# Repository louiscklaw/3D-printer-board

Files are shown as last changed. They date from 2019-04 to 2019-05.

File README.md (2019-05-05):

### PCB tryout for louis 3d printer
* PCB look like:
	* front:
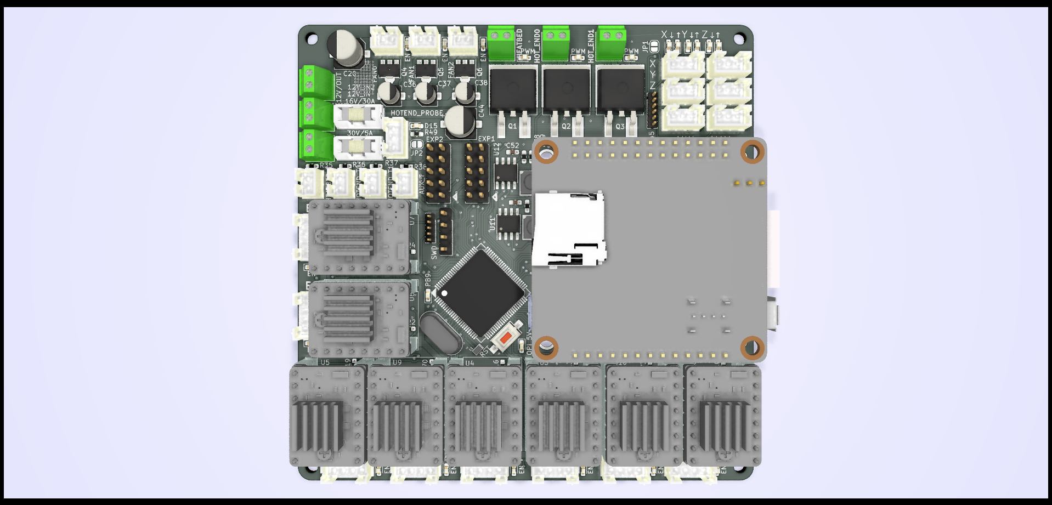
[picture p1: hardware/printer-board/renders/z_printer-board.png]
PCB Front Front
	

	* back:
	PCB Back Back

### to initialize the stm32 with klipper firmware
* to flash klipper with stm32duino: 
    * `wget 'https://github.com/rogerclarkmelbourne/STM32duino-bootloader/raw/master/binaries/generic_boot20_pc13.bin'`
    * `st-flash /home/logic/_del/7/generic_boot20_pc13.bin 0x8000000`
    * `dfu-util -d 1eaf:0003 -a 2 -R -D out/klipper.bin`

* to flash klipper by st-link
    * `st-flash write klipper.out 0x8000000`

ref: https://github.com/KevinOConnor/klipper/blob/master/docs/Bootloaders.md

### TODO on this REV:
- [x] tidy
- [x] need to confirm about ~~PC13~~ PB9 as debug pin

### Design goal on REV1:
- [x] ~~10~~ 8 channels and ~~10~~ 8 stepper motors
    - [x] x
    - [x] y
    - [x] z0,z1,z2,z3
    - [x] e0,e1,~~e2,e3~~

- [x] ~~5~~ 3 channels PWM control(high power) heaters
    - [x] hotend0, hotend1, ~~hotend2, hotend3~~
    - [x] heatbed

- [x] ~~5~~ 3 channels PWM control(low power) fans
    - [x] hotend0, hotend1, ~~hotend2, hotend3~~
    - [x] heatbed

- [x] 6 and ~~4~~ 1 DI
    - [x] x,y,z min
    - [x] x,y,z max
    - [x] ~~4 misc~~ 
    - [x] PROBE support

- [x] ~~5~~ 4 + 1  AI(temperature sensors)
    - [x] hotend0,hotend1,~~hotend2,hotend3~~, AUX
    - [x] heatbed
    - [x] PCB temperature self monitoring

### Board source current estimation (**Rough/TBC**):
* stepper motors = 10 * 0.5A ~= 5A
* heatbed = 150W/12 ~= 12A
* hotends = 2 * 20W = 80W ~= 3A

* 12 + 5 + 3 = 20A
* guess taking 0.5 as Diversity factor => 10A

### Thing TODO on next REV:
- [ ] replacement for Orange Pi as too big in size
- [ ] I2C output
- [ ] possibily some digital output channel
- [ ] possibily some SSR channel

### Misc:
* pinmapping
    * https://github.com/KevinOConnor/klipper/blob/master/docs/stm32f1.md

* Constrains on STM32:
> When using serial, the UART used for communication with the host is fixed to pins PA9 (TX) and PA10 (RX). 
> When using USB, the PA11 (D-) and PA12 (D+) pins are reserved. 
> The USB code assumes that PA12 (D+) has a fixed pullup resistor attached to it.

> SWD pins (PA13/PA14) are enabled for debugging and cannot be used for any I/O. 
> SPI uses pins PB13/PB14/PB15, but the pins can be used as general I/O if SPI is not used.
> Digital I/O

> All pins that aren't part of the fixed set can be used for digital I/O. 
> Pins are referred to by their primary name, e.g. PA1. 
> Do not try to use Arduino pin aliases in your configuration. 
> See ST's datasheets for more details. 
> The STM32Duino wiki has more info on the popular "Blue Pill" board.
> Analog inputs

> All ADC-capable pins can be used as analog inputs with the same naming as digital I/O pins. 
> Small packages MCUs (e.g. LFQP48) have 10 channels (PA0-PA7, PB0-PB1), while larger package devices have 16 channels (PA0 PA7, PB0-PB1, PC0-PC5).

> SPI
> SPI uses pin PB13 (SCK), PB14 (MISO) and PB15 (MOSI). The clock speed range is 0.15..18 MHz.  Chip select pins do not have any restrictions.

ref: https://github.com/KevinOConnor/klipper/blob/master/docs/stm32f1.md

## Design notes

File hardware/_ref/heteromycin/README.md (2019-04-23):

# Heteromycin - 3D printer board

[Join us on Discord!](https://discord.gg/f4dmGsn)

Heteromycin is a 3D printer controller that aims to provide a full stack user
experience around Octoprint / Marlin using a custom designed board that
integrates a Raspberry Pi 3 or Zero W. It will also provide a solid, powerfull
hardware by utilizing quality components, a STM32 32bit MCU and powerfull
TMC5160 or TMC2160 driver (SD / SPI mode).

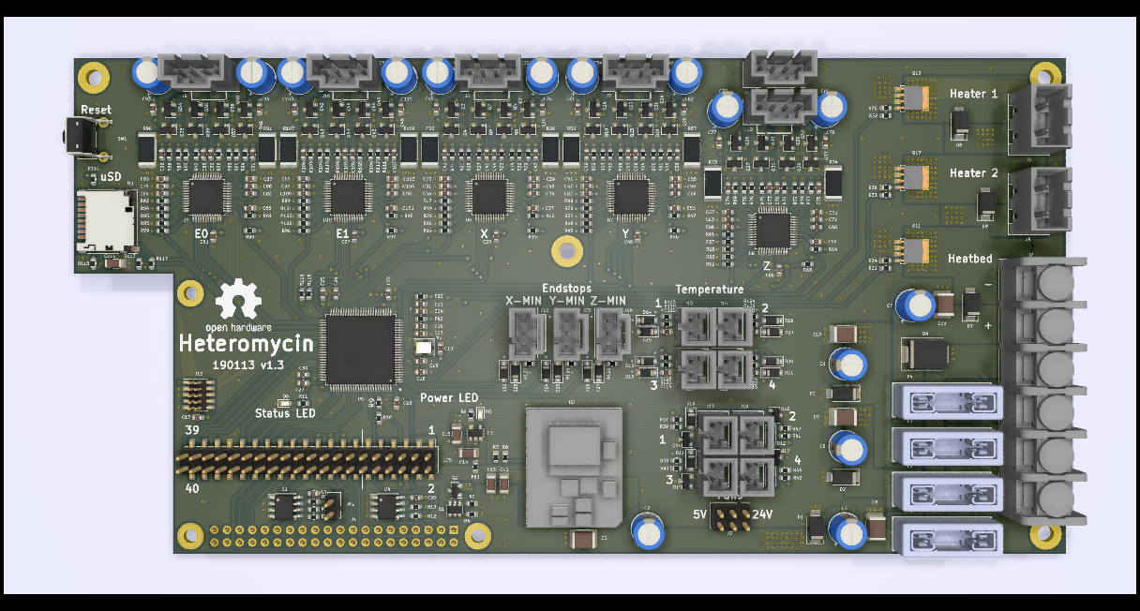
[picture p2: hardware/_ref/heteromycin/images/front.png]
heteromycin version 1.0


## Features

* 32bit STM32H743VI 400Mhz / 1024KiB RAM / 2MiB Flash MCU / 4 KiB EEPROM
* Integrated Raspberry Pi 3 / Zero W HAT connector as the main user interface
* Integrated DC/DC switching module for 5V / 3.3V power supply
* 5x TMC5160 or TMC2160 stepper driver with 8x external Power MOSFET each
* 3x high power MOSFET for heating (2x heater, 1x heatbed, 24V)
* 4x low power MOSFET for fans (5V or 24V)
* 40 pin external connector for STM32 and Pi GPIO pins
  * GPIO
  * PWM
  * UART
  * SPI
  * I2C
  * 3.3V / 5V / GND for external power consumption
* Micro SD Card for storing GCODE files (directa MCU access)
* Designed for a 24V power supply
* Automotive fuses
* Quality connectors
* Octoprint plugin for flashing the firmware of the board (STM32)

## Roadmap

* Hardware
  * [x] Describe the general functionality and select the main components
  * [x] Draw the schematics of the PCB
  * [x] Placement & routing of the PCB
  * [ ] Production of a development board
  * [ ] Testing the PCB
  * [ ] Repreat until hardware is finished
* Software
  * [x] Write arduino core board definition once first PCB design is finished
  * [ ] Write PIN file for Marlin
  * [ ] Test board (esp. the TMC*160 driver)
  * [ ] Octoprint plugin for firmware upgrade
  * [ ] STM32flash rewrite (fix I2C and add SPI, maybe rewrite in rust)
  * [ ] Create a script / image with Octoprint with the plugin / tools
  preinstalled
  * [ ] Documentation

## Alternative Parts

### Stepper driver

You can use both TMC5160 or TMC2160 as the stepper driver, since they both are
functionally / pin equal when used in SD / SPI-Mode.

It doesn't mater choosing one over the other, other than price and availability.

Fine tuning of the MOSFET driver may be necessary.

## License

The hardware is licensed under CERN OHL version 1.2.
The software is licensed under GNU GPL v3.

The files under PCB/packages3d are excluded from this license and are provided
under fair use terms for this open-source project.

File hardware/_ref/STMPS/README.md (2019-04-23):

STMPS
=====

**STMPS** is a WIP 3d printer board based around the STM32f411, with inspiration and guidance
from the Printrboard, RAMPS 1.4, and the RepRap project.

**ALPHA-3**

a3

This board is intended to work with Ambroz Bizjak's astonishingly fantastic 
[aprinter](https://github.com/ambrop72/aprinter) firmware. Configuration files and guidance will be
provided once the board is further along.

STMPS is open source hardware, licensed under CC BY-SA. Copyright (C) 2016 Greg Lincoln.

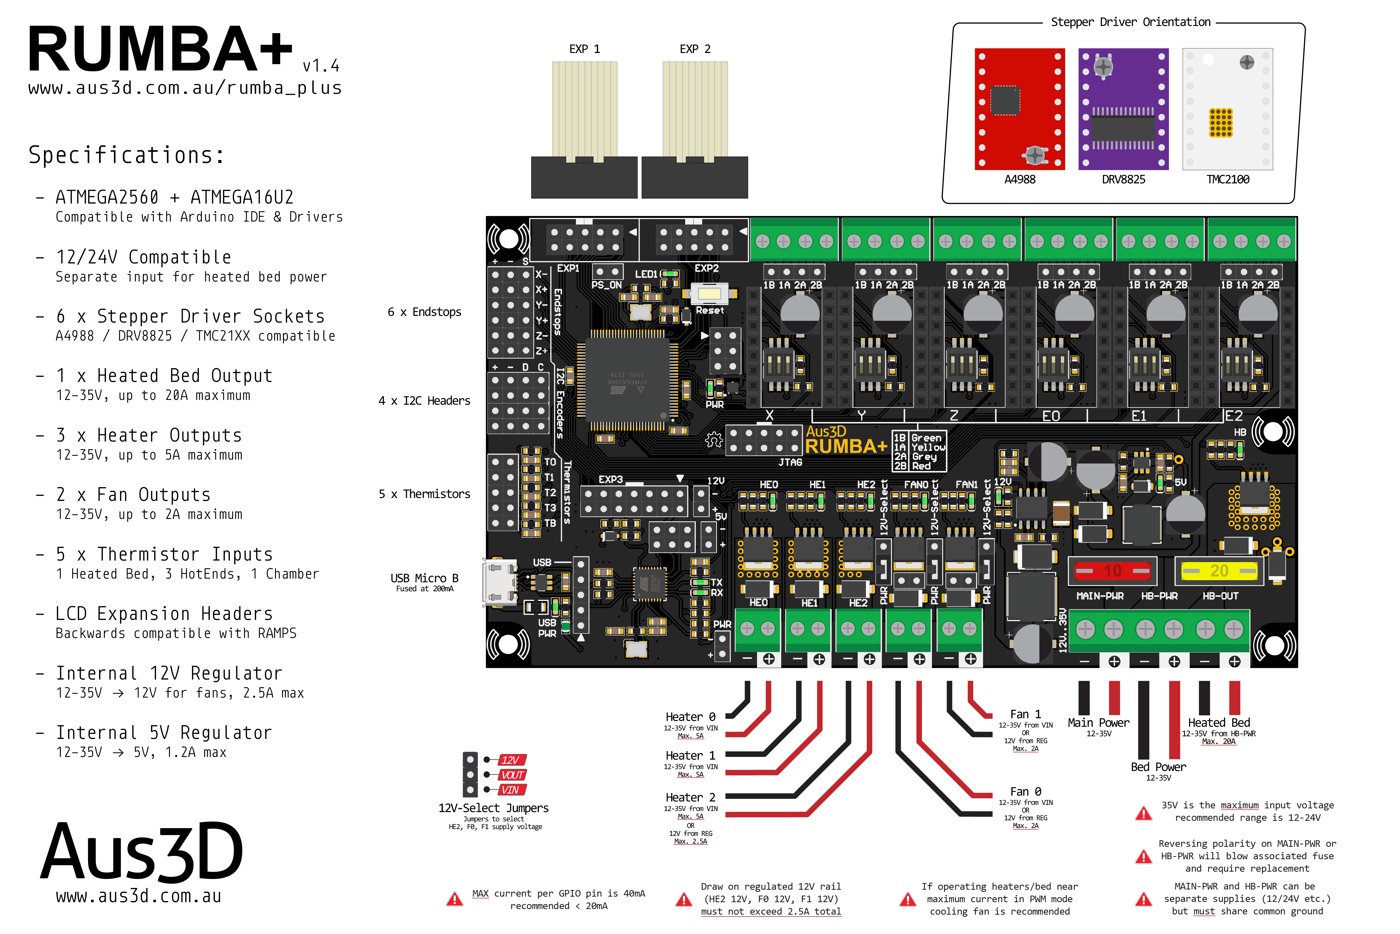
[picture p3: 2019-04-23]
hardware/_ref/RUMBA-Plus/Images/pinOut.png

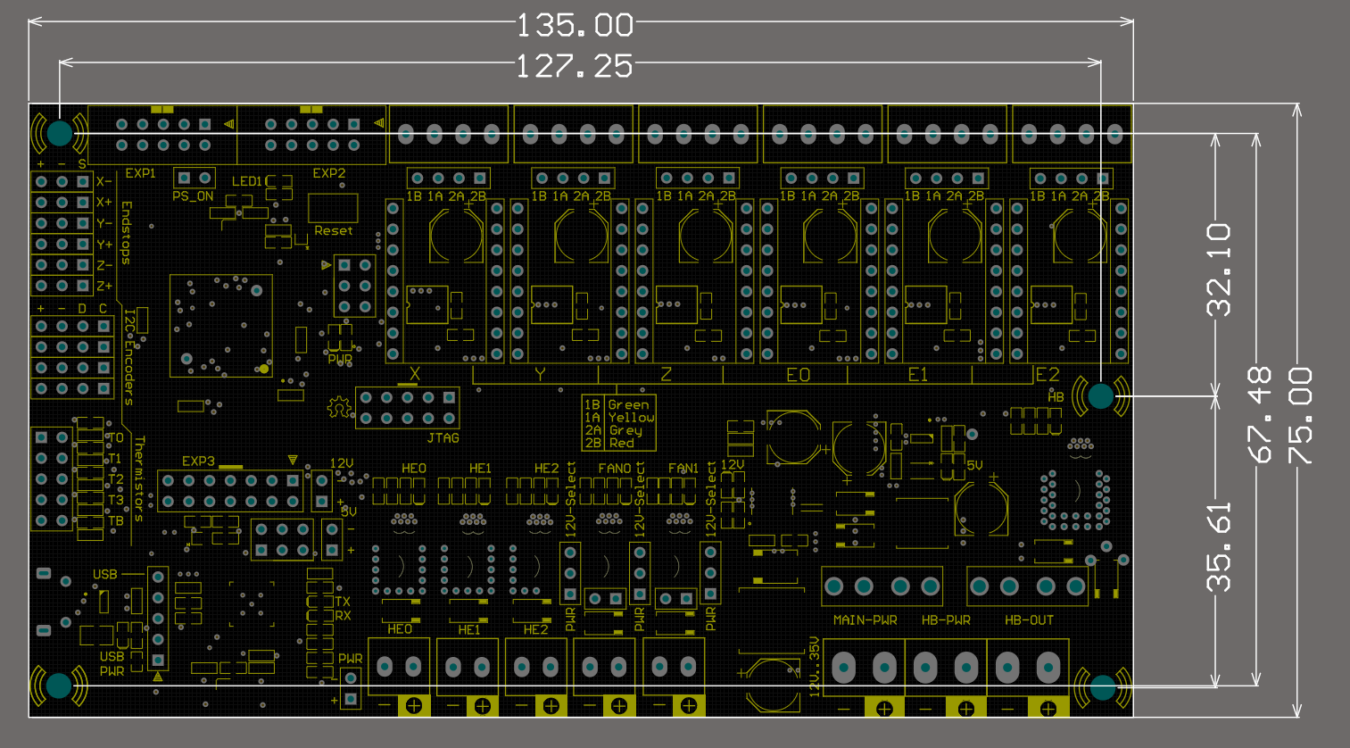
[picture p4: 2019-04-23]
hardware/_ref/RUMBA-Plus/Images/BoardMountingDimension.png

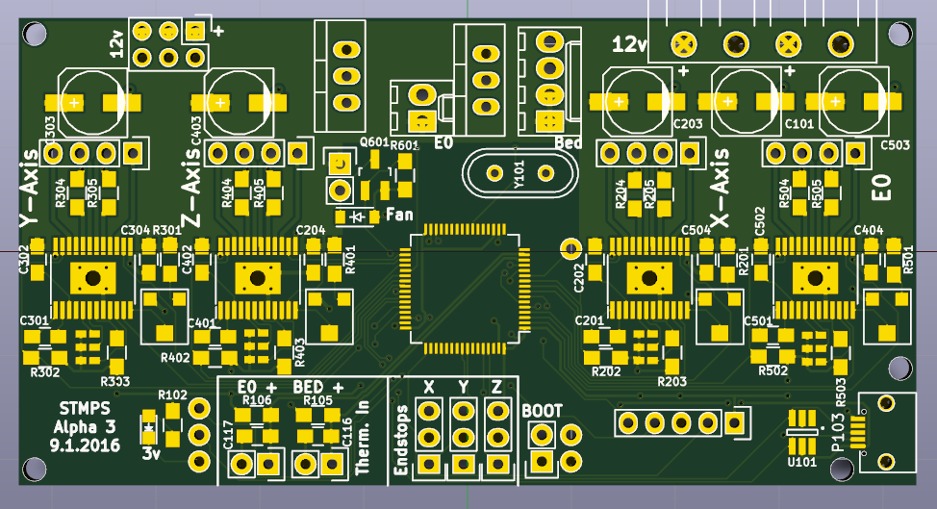
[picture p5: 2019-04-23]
hardware/_ref/STMPS/img/stmps-a3.png

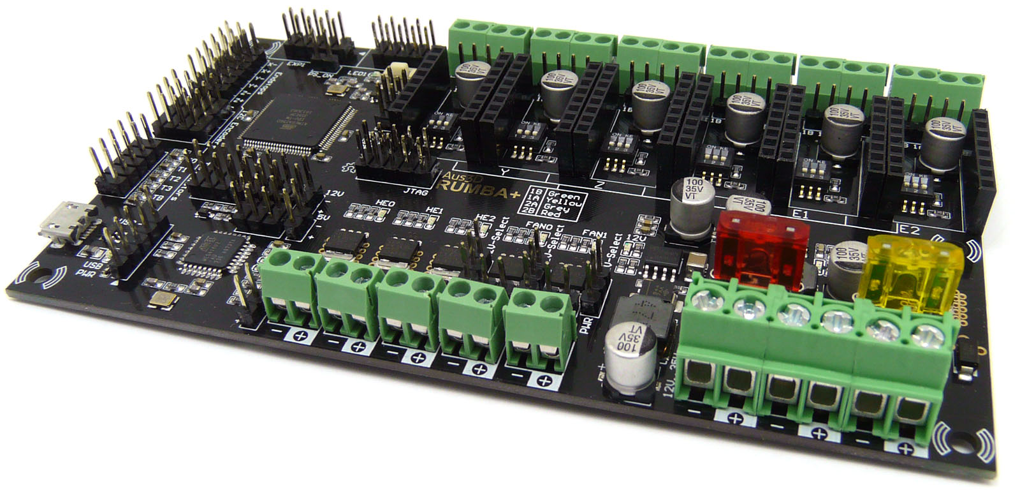
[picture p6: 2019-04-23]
hardware/_ref/RUMBA-Plus/Images/boardPhoto.jpg

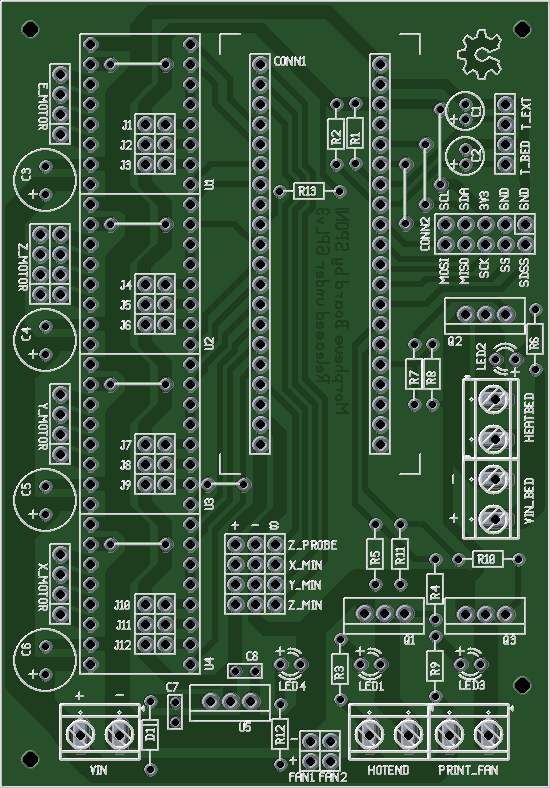
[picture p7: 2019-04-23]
hardware/_ref/Morpheus-STM32/documents/board.png

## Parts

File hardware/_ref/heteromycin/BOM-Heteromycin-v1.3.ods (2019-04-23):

Reference(s) | Value | Mft. Nr. | Digikey Nr. | Mouser Nr. | LCSC Nr. | Qty | Footprint | Note | Datasheet
C1, C16, C17, C18, C19, C22, C23, C24, C25, C26, C27, C29, C31, C33, C39, C40, C47, C49, C55, C56, C63, C65, C71, C72, C79, C81, C87, C88, C95, C97, C103, C104, C112, C113, C114, C115 | 100nF | C0603C104M5RACTU | C0603C104M5RACTU | 81-GCM188L81H104KA7D | C42998 | 36 | Capacitor_SMD:C_0603_1608Metric | Min. 35V | ~
C2, C4, C5, C6, C7, C32, C38, C48, C54, C64, C70, C80, C86, C96, C102 | 100uF | 860020573008 | 732-8942-1-ND | 710-860020573008 |  | 15 | Capacitor_SMD:CP_Elec_6.3x5.7 | Min. 35V
C3, C8, C9, C10, C11 | 100nF | VJ1812Y104KXBAT | 478-4009-1-ND | 77-VJ1812Y104KXBAT | C106148 | 5 | Capacitor_SMD:C_1812_4532Metric | Min. 35V
C12, C14 | 22uF | LMK316ABJ226KL-T | 1276-1771-2-ND | 963-LMK316ABJ226KL-T | C92818 | 2 | Capacitor_SMD:C_1206_3216Metric | Min. 6V | ~
C13 | 100nF | VJ1206Y104JXQCW1BC | 732-12245-1-ND | 77-VJ1206Y104JXQCBC | C313097 | 1 | Capacitor_SMD:C_1206_3216Metric | Min. 6V | ~
C15, C111 | 10uF | EMK316BJ106MD-T | 1276-2877-1-ND | 963-EMK316BJ106MD-T | C50691 | 2 | Capacitor_SMD:C_1206_3216Metric | Min. 6V | ~
C20, C21 | 1uF | 885012106022 | 1276-6524-1-ND | 710-885012106022 | C95843 | 2 | Capacitor_SMD:C_0603_1608Metric | Min. 6V | ~
C28, C30, C35, C36, C51, C52, C67, C68, C83, C84, C99, C100 | 2.2uF | CGB3B1X5R1C225M055AC | 587-4861-1-ND | 810-CGB3B1X5R1C225MC | C106832 | 12 | Capacitor_SMD:C_0603_1608Metric | Min. 16V | ~
C34, C50, C66, C82, C98 | 22nF | C0603C223K1RACTU | 399-3476-1-ND | 80-C0603C223K1R | C77443 | 5 | Capacitor_SMD:C_0603_1608Metric | Min. 100V | ~
C37, C45, C46, C53, C61, C62, C69, C77, C78, C85, C93, C94, C101, C109, C110 | 470nF | GMK107B7474KAHT | 445-172475-1-ND | 963-GMK107B7474KAHT | C296719 | 15 | Capacitor_SMD:C_0603_1608Metric | Min. 35V | ~
C41, C42, C43, C44, C57, C58, C59, C60, C73, C74, C75, C76, C89, C90, C91, C92, C105, C106, C107, C108 | 220nF | GMK107BJ224KAHT | 490-12546-1-ND | 963-GMK107BJ224KAHT | C123521 | 20 | Capacitor_SMD:C_0603_1608Metric | Min. 35V | ~
D1, D2, D3 | SMAJ28A | SMAJ28A-13-F | SMAJ28A-FDICT-ND | 621-SMAJ28A-13-F | C353458 | 3 | Diode_SMD:D_SMA |  | https://www.mouser.de/datasheet/2/240/Littelfuse_TVS_Diode_SMAJ_Datasheet.pdf-540740.pdf
D4 | S3A-13-F | S3A-13-F | S3A-FDITR-ND | 621-S3A-F | C264105 | 1 | Diode_SMD:D_SMC |  | https://www.mouser.de/datasheet/2/115/ds16005-37880.pdf
D5 | LTST-C194KGKT | LTST-C194KGKT | 160-1834-1-ND | 859-LTST-C194KGKT | C125098 | 1 | LED_SMD:LED_0603_1608Metric |  | ~
D6 | LTST-C194KSKT | LTST-C194KSKT | 160-1836-1-ND | LTST-C194KSKT | C84268 | 1 | LED_SMD:LED_0603_1608Metric |  | ~
D7, D8, D9 | SK310A-LTP | SK310A-LTP | SK310A-LTPMSCT-ND | 833-SK310A-LTP | C91474 | 3 | Diode_SMD:D_SMA |  | https://www.mouser.de/ProductDetail/Micro-Commercial-Components-MCC/SK310A-TP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
D10, D11, D12, D13, D14, D15, D16, D17, D18, D19, D20, D21, D22, D23, D24, D25, D26, D27 | BAT54GWJ | BAT54GWJ | 1727-7328-1-ND | 841-BAT54GWJ |  | 18 | Diode_SMD:D_SOD-123 |  | https://www.mouser.de/datasheet/2/916/BAT54GW-1318921.pdf
F1, F2, F3, F4 | 3557-2 | 3557-2 | 36-3557-2-ND | 534-3557-2 |  | 4 | heteromycin:KEYSTONE-FUSE-3557-2 |  | ~
FB1, FB2, FB3 | MPZ1608S221A | MPZ1608S221A | 445-1565-2-ND | 810-MPZ1608S221A | C76815 | 3 | Resistor_SMD:R_0603_1608Metric |  | https://www.mouser.de/datasheet/2/400/eads_commercial_power_mpz1608_en-923650.pdf
J1 | M20-7832046 | M20-7832046 | 952-2150-ND | 855-M20-7832046 |  | 1 | Connector_PinSocket_2.54mm:PinSocket_2x20_P2.54mm_Vertical
J2 | 4DB-P108-06 | 4DB-P108-06 | 4DB-P108-06 | 571-214376679 |  | 1 | heteromycin:4DB-P108-06 | Alternative: OSTYK42106030 | https://www.mouser.de/datasheet/2/418/NG_CD_2-1437667-4_N8-639207.pdf
J3, J4 | 039531-1002 | 039531-1002 | WM7837-ND | 538-39531-1002 |  | 2 | heteromycin:39531-1002 |  | ~
J5 | 68602-406HLF | 68602-406HLF | 609-4934-ND | 649-68602-406HLF | C124384 | 1 | Connector_PinHeader_2.54mm:PinHeader_2x03_P2.54mm_Vertical |  | ~
J6, J7, J8, J9, J10, J21 | 70543-0003 | 70543-0003 | WM4802-ND | 538-70543-0003 |  | 6 | heteromycin:70543-0003 |  | https://www.mouser.de/ProductDetail/Molex/70543-0003
J11 | DM3D-SF | DM3D-SF | HR1941CT-ND | 798-DM3D-SF |  | 1 | Connector_Card:microSD_HC_Hirose_DM3D-SF |  | https://www.hirose.com/product/en/download_file/key_name/DM3/category/Catalog/doc_file_id/49662/?item_id=195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
J12 | 20021121-00010C4LF | 20021121-00010C4LF | 609-3695-1-ND | 649-202112100010C4LF |  | 1 | Connector_PinHeader_1.27mm:PinHeader_2x05_P1.27mm_Vertical_SMD |  | https://www.mouser.de/datasheet/2/18/20021121-1362884.pdf
J13, J14, J15, J16, J17, J18, J19, J20 | 70543-0001 | 70543-0001 | WM4800-ND | 538-70543-0001 |  | 8 | heteromycin:70543-0001 |  | https://www.mouser.de/ProductDetail/Molex/50-57-9402
J22, J23, J24 | 70543-0002 | 70543-0002 | WM4801-ND | 538-70543-0002 |  | 3 | heteromycin:70543-0002 |  | ~
J25 | 95157-140LF | 95157-140LF | 609-2231-ND | 649-95157-140LF |  | 1 | Connector_PinHeader_2.54mm:PinHeader_2x20_P2.54mm_Vertical_SMD |  | ~
JP1 | Jumper_2_Open | M20-9990246 | 952-2262-ND | 855-M20-9990246 | C124375 | 1 | Connector_PinHeader_2.54mm:PinHeader_1x02_P2.54mm_Vertical |  | ~
Q1 | DMMT5401 | DMMT5401 | DMMT5401-FDICT-ND | DMMT5401-7-F | C154733 | 1 | Package_TO_SOT_SMD:SOT-23-6
Q2 | DMG2305UX | DMG2305UX | DMG2305UX-13DICT-ND | 621-DMG2305UX-7 | C144153 | 1 | Package_TO_SOT_SMD:SOT-23 |  | https://www.diodes.com/assets/Datasheets/DMG2305UX.pdf
Q3, Q4, Q5, Q6, Q7, Q8, Q9, Q10, Q14, Q15, Q16, Q17, Q18, Q19, Q20, Q21, Q22, Q23, Q24, Q25, Q26, Q27, Q28, Q29, Q30, Q31, Q32, Q33, Q34, Q35, Q36, Q37, Q38, Q39, Q40, Q41, Q42, Q43, Q44, Q45, Q46, Q47, Q48, Q49 | IRLML0030TRPbF | IRLML0030TRPbF | IRLML0030TRPBFCT-ND | 942-IRLML0030TRPBF | C67272 | 44 | Package_TO_SOT_SMD:SOT-23 |  | https://www.infineon.com/dgdl/irlml0030pbf.pdf?fileId=5546d462533600a401535664773825df
Q11, Q12, Q13 | PSMN1R2-30YLC,115 | PSMN1R2-30YLC,115 | 1727-5295-1-ND | 771-PSMN1R230YLC115 | C134469 | 3 | heteromycin:SOT-669_LFPAK_ThermalVias-1 | Alternatives: PSMN1R8-40YLC,115; PSMN1R3-30YL,115 PSMN1R5-30YLC | https://assets.nexperia.com/documents/data-sheet/PSMN1R2-30YLC.pdf
R1, R5, R14, R15, R45, R46, R62, R63, R79, R80, R96, R97, R113, R114, R115, R116, R117, R118 | 47k | CR0603-FX-4702ELF | CR0603-FX-4702ELFTR-ND | 652-CR0603FX-4702ELF | C279997 | 18 | Resistor_SMD:R_0603_1608Metric |  | ~
R2, R3 | 3.9K | RC0603FR-103K9L | 311-3.90KHRCT-ND | 603-RC0603FR-103K9L | C25997 | 2 | Resistor_SMD:R_0603_1608Metric
R4, R9 | 10k | AC0603FR-0710KL | P10.0KHCT-ND | 603-AC0603FR-0710KL | C99198 | 2 | Resistor_SMD:R_0603_1608Metric |  | ~
R6 | 20k | RC0603FR-1020KL | YAG3577CT-ND | 603-RC0603FR-1020KL | C118368 | 1 | Resistor_SMD:R_0603_1608Metric |  | ~
R7 | 15k | RC0603FR-0715KL | 311-15.0KHRCT-ND | 603-RC0603FR-0715KL | C25581 | 1 | Resistor_SMD:R_0603_1608Metric |  | ~
R8, R11, R127, R128, R129 | 1k | RC0603JR-7W1KL | YAG2323CT-ND | 603-RC0603JR-7W1KL | C25585 | 5 | Resistor_SMD:R_0603_1608Metric |  | ~
R12, R13, R119, R120, R121, R122, R123, R124, R125, R126 | 4.7k | AC0603JR-074K7L | YAG3676CT-ND | 603-AC0603JR-074K7L | C25999 | 10 | Resistor_SMD:R_0603_1608Metric |  | ~
R16, R47, R64, R81, R98 | 2.2 | CRCW06032R20FKEA | 541-2.20SCT-ND | 71-CRCW0603-2.2-E3 | C25226 | 5 | Resistor_SMD:R_0603_1608Metric | Can also be 3.3 Ohm | ~
R17, R18, R19, R20, R48, R49, R50, R51, R65, R66, R67, R68, R82, R83, R84, R85, R99, R100, R101, R102 | 47 | RC0603FR-1047RL | A129672CT-ND | 603-RC0603FR-1047RL | C114623 | 20 | Resistor_SMD:R_0603_1608Metric |  | ~
R21, R22, R23, R24, R27, R28, R29, R30, R52, R53, R54, R55, R58, R59, R60, R61, R69, R70, R71, R72, R75, R76, R77, R78, R86, R87, R88, R89, R92, R93, R94, R95, R103, R104, R105, R106, R109, R110, R111, R112 | 10 | SFR03EZPF10R0 | RC0603FR-0710RL | 755-SFR03EZPF10R0 | C304686 | 40 | Resistor_SMD:R_0603_1608Metric |  | ~
R25, R26, R56, R57, R73, R74, R90, R91, R107, R108 | 0.1 | PE2512FKE070R1L | YAG2159CT-ND | 603-PE2512FKE070R1L | C159168 | 10 | Resistor_SMD:R_2512_6332Metric | 0.5 or 1W
R31, R32, R33, R37, R38, R41, R42 | 100 | RC0603FR-7W100RL | RMCF0603FG100RTR-ND | 603-RC0603FR-7W100RL | C25201 | 7 | Resistor_SMD:R_0603_1608Metric |  | ~
R10, R34, R35, R36, R39, R40, R43, R44 | 100k | CRCW0603100KFKEAC | 541-3950-1-ND | 71-CRCW0603100KFKEAC | C103211 | 8 | Resistor_SMD:R_0603_1608Metric |  | ~
SW1 | PTS645VL39-2 | PTS645VL392LFS | CKN9103-ND | 611-PTS645VL392 | C221891 | 1 | Button_Switch_THT:SW_Tactile_SPST_Angled_PTS645Vx39-2LFS |  | https://www.mouser.de/datasheet/2/60/-1131575.pdf
U1, U4 | CAT24C32 | CAT24C32WI-GT3 | CAT24C32WI-GT3CT-ND | 698-CAT24C32WI-GT3 | C81193 | 2 | Package_SO:SOIC-8_3.9x4.9mm_P1.27mm
U2 | I3A4W008A033V-001-R | I3A4W008A033V-001-R | 285-2720-ND | 967-I3A4W008A033V01R |  | 1 | heteromycin:i3A |  | https://www.us.tdk-lambda.com/ftp/specs/i3a_full_datasheet.pdf
U3 | AP7365-33WG-7 | AP7365-33WG-7 | AP7365-33WG-7DICT-ND | 621-AP7365-33WG-7 | C150742 | 1 | Package_TO_SOT_SMD:SOT-23-5 |  | https://www.mouser.de/datasheet/2/115/AP7365-86154.pdf
U5 | STM32H743VI | STM32H743VI | 497-17720-ND | 511-STM32H743VIT6 |  | 1 | heteromycin:TQFP-100_14x14mm_P0.5mm |  | https://www.st.com/en/microcontrollers/stm32h743vi.html
U6, U7, U8, U9, U10 | TMC2160-TA | TMC2160-TA | TMC2160-TA | - |  | 5 | heteromycin:TQFP-48-1EP_7x7mm_P0.5mm_EP5x5mm_ThermalVias | Not available at Mouser | https://www.trinamic.com/fileadmin/assets/Products/ICs_Documents/TMC5160_Datasheet_V1.01.pdf
X1 | ECS-TXO-3225-250-TR | ECS-TXO-3225-250-TR | XC2062CT-ND | 520-TXO-3225-25.0T |  | 1 | heteromycin:ECS-TXO-3225 |  | https://www.ecsxtal.com/store/pdf/ECS-TXO-3225.pdf
Jumper | Jumper | M7581-46 | S9337-ND | 855-M7581-46 |  | 3

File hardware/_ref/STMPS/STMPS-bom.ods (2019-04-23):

Reference | Quantity | Value | Footprint | MPN
C101 C203 C303 C403 C503 | 5 | 100uf | Capacitors_SMD:c_elec_6.3x5.8 | 35TZV100M6.3X8
C102 C116 C117 | 3 | 10uf | Capacitors_SMD:C_0805_HandSoldering
C103 C104 | 2 | 20pf | Capacitors_SMD:C_0805_HandSoldering
C109 | 1 | 1uf | Capacitors_SMD:C_0805_HandSoldering
C113 C114 | 2 | 4.7uf | Capacitors_SMD:C_0805_HandSoldering
C118 C201 C202 C204 C301 C302 C304 C401 C402 C404 C501 C502 C504 C105 C106 C107 C108 C110 C111 C112 | 20 | 0.1uf | Capacitors_SMD:C_0805_HandSoldering
D101 | 1 | 12v_PWR | LEDs:LED_0805
D102 | 1 | 3v_PWR | LEDs:LED_0805
D601 | 1 | D_Schottky_Small | Diodes_SMD:SOD-123 | DB2J41100L | DB2X41100L
D701 D801 | 2 | r | LEDs:LED_0805
P101 | 1 | 12v IN | stmps:5EHDRC_1x04 |  | Tayda
P102 | 1 | 12v | Pin_Headers:Pin_Header_Straight_2x03 |  | Tayda
P103 | 1 | USB_OTG | Connect:USB_Micro-B
P104 | 1 | E0_THERM | Pin_Headers:Pin_Header_Straight_1x02 |  | Tayda
P105 | 1 | X_STOP | Pin_Headers:Pin_Header_Straight_1x03 |  | Tayda
P106 | 1 | SWD | Pin_Headers:Pin_Header_Straight_1x06 |  | Tayda
P107 | 1 | BED_THERM | Pin_Headers:Pin_Header_Straight_1x02 |  | Tayda
P108 | 1 | Y_STOP | Pin_Headers:Pin_Header_Straight_1x03 |  | Tayda
P109 | 1 | Z_STOP | Pin_Headers:Pin_Header_Straight_1x03 |  | Tayda
P201 P301 P401 P501 | 4 | MOT | Pin_Headers:Pin_Header_Straight_1x04 |  | Tayda
P601 | 1 | LP_OUT | Pin_Headers:Pin_Header_Straight_1x02 |  | Tayda
P701 P801 | 2 | OUT | Connectors_Molex:Molex_KK-6410-02_02x2.54mm_Straight |  | Tayda
Q601 | 1 | SSM3K333 | TO_SOT_Packages_SMD:SOT-23_Handsoldering | SSM3K333RLFCT-ND
Q701 Q801 | 2 | IPP039N04L | TO_SOT_Packages_THT:TO-220_Neutral123_Vertical | IPP039N04LGXKSA1-ND | Tayda
R101 R703 R803 | 3 | 560 | Resistors_SMD:R_0805_HandSoldering
R102 | 1 | 56 | Resistors_SMD:R_0805_HandSoldering
R103 | 1 | 220 | Resistors_SMD:R_0805_HandSoldering
R104 R202 R203 R302 R303 R402 R403 R502 R503 R601 R701 R801 | 12 | 100k | Resistors_SMD:R_0805_HandSoldering
R105 R106 R107 R108 | 4 | 4.7k | Resistors_SMD:R_0805_HandSoldering
R201 R301 R401 R501 | 4 | 200k | Resistors_SMD:R_0805_HandSoldering
R204 R205 R304 R305 R404 R405 R504 R505 | 8 | 0.1 | Resistors_SMD:R_0805_HandSoldering
R702 R802 | 2 | 100 | Resistors_SMD:R_0805_HandSoldering
RV201 RV301 RV401 RV501 | 4 | 100k | stmps:BOURNS-TC33X-2 | TC33X-2-104E
U101 | 1 | AOZ8904 | TO_SOT_Packages_SMD:SOT-23-6_Handsoldering | AOZ8904CIL
U102 | 1 | LM1117-3.3v | TO_SOT_Packages_SMD:TO-252-2Lead
U103 | 1 | STM32F411RCTx | Housings_QFP:LQFP-64_10x10mm_Pitch0.5mm | STM32F411RCT6 | Future
U104 | 1 | M24C04 | Housings_SOIC:SOIC-8_3.9x4.9mm_Pitch1.27mm | M24C04-WMN6TP
U201 U301 U401 U501 | 4 | A5984 | stmps:TSSOP-24_4.4x7.8mm_Pitch0.65mm | A5984GLPTR-T
Y101 | 1 | Crystal | Crystals:Crystal_HC49-U_Vertical | ABL-8.000MHZ-B2 | Tayda

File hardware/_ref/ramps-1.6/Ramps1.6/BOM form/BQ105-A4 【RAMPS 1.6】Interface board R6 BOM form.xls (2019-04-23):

BQ105-A4【RAMPS 1.6】主板接口板R6 BOM表
物料编码 | 元件型号 | 元件丝印 | 封装 | 数量 | 备注
DDR000001 | 0.1UF/50V | C1 | 0603N | 1 | 贴片电容
DDR000012 | 35V/100UF | C2, C6, C7, C8, C9, C10 | 35V/100UF-2 | 6 | 贴片电容
DDR000040 | 35V/10UF | C3, C4, C5 | 35V/10UF | 3 | 贴片电容
DRJ000005 | IN4004【M4】 | D1, D2 | DO-214AC | 2 | 贴片二极管
DLE000008 | LED | D3, D4, D5, D6 | LED-0603 | 4 | 贴片蓝灯
DBX000003 | 30A【16V 30A】 | F1 | 1206 | 1 | 贴片保险丝
DBX000007 | MFR500 【30V 5A】 | F2 | 1206 | 1 | 贴片保险丝
DPZ000029 | SIP36 | J1 | 2.54-36 | 1 | 插件双排排针
DPZ000032 | AUX-4 | J2 | SIP18 | 1 | 插件单排排针
DPZ000027 | SER1 | J3 | SIP3 | 1 | 插件单排4P排针 + 插件Header2*4P
 | SER2 | J7 | SIP3 | 1
DPZ000025 | SER3 | J11 | SIP3 | 1
 | SER4 | J13 | SIP3 | 1
 | 12V-AUX | J4 | SIP2 | 1 | 不装
DPZ000031 | 3P | J5 | SIP3 | 1 | 插件单排排针
DPZ000025 | SERIAL | J6 | 2.54-4 | 1 | 插件Header2*4P
 | A-OUT | J12 | 2.54-4 | 1
DPZ000026 | AUX-2 | J8 | Header2*5 | 1 | 插件双排排针
DPZ000025 | AUX-3 | J9 | Header4*2 | 1 | 插件双排排针
DPZ000008 | 300V/20A | J10, J28 | 5.08-2 | 2 | 插件电源端子
DPZ000027 | X-MOT | J14 | SIP4 | 1 | 插件单排排针
 | Y-MOT | J15 | SIP4 | 1
 | Z-MOT | J16, J17 | SIP4 | 2
 | E0-MOT | J18 | SIP4 | 1
 | E1-MOT | J25 | SIP4 | 1
 | I2C | J29 | SIP4 | 1
DPZ000002 | X- | J19 | SIP3 | 1 | 插件单排6P排针+插件Header2*6P
 | X+ | J20 | SIP3 | 1
 | Y- | J21 | SIP3 | 1
DPZ000030 | Y+ | J22 | SIP3 | 1
 | Z- | J23 | SIP3 | 1
 | Z+ | J24 | SIP3 | 1
DPZ000113 | 5.08-4 | J26 | 5.08-4-B | 1 | 插件接线端子
DPZ000002 | 6P | J27 | 2.54-6 | 1 | 插件单排针座
DPZ000009 | JP6 | JK1, JK2, JK3, JK4, JK5 | Header3*2 | 5 | 插件双排针座
DPZ000001 | 8P | JM1, JM2, JM3, JM4, JM6 | SIP8 | 5 | 插件单排针座
DPZ000002 | 6P | JM5 | SIP6 | 1 | 插件单排针座
DKG000003 | RESET | K1 | K7 | 1 | 插件复位开关
DSJ000006 | STP55NF06 | Q1, Q2 | TO-263-M | 2 | 贴片MOS管
DSJ000008 | WSK220N04 | Q3 | TO-263-M | 1 | 贴片MOS管
DDZ000004 | 100K/±1% | R1, R3, R5, R7, R9, R13, R17, R23 | 0603N | 8 | 贴片电阻
DDZ000006 | 10K/±1% | R2, R4, R6, R8, R10 | 0603N | 5 | 贴片电阻
DDZ000024 | 10R/±1% | R11, R15, R19 | 0603N | 3 | 贴片电阻
DDZ000023 | 1.8K/±1% | R12, R16, R18 | 0603N | 3 | 贴片电阻
DDZ000005 | 1K/±1% | R14 | 0603N | 1 | 贴片电阻
DDZ000008 | 4.7K/±1% | R20, R21, R22, R24, R25 | 0603N | 5 | 贴片电阻
DIC000001 | A4988 | U1, U2, U3, U4, U5 | A4988-2 | 5 | 单排母16P插座2个+单排母24P插座2个
WSR000019 | 散热器 | 【长60MM*宽10MM*高10MM】 |  | 1 | 客户自选配件 【如果热床≤1Ω建议用】
DPC000096 | PCB | BQ105-A4【RAMPS 1.6】 |  | 1 | 空板
 | 制表：李荣强 |  | 时间: 2017.12.12

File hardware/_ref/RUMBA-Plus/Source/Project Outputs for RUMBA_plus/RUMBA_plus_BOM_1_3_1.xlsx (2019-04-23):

Designator | Description | Comment | Value | Quantity | Note | Manufacturer 1 | Manufacturer Part Number 1 | Supplier 1 | Supplier Part Number 1
5V, 12V, FAN0_1, FAN1_1, PS_ON, PWR | Header, 2-Pin | Header 2 |  | 6 | Approved sub OK | Generic Header (https://octopart-clicks.com/click/altium?sku=3M9447-ND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)
C1, C2, C21, C22, C23, C24, C25, C30, C31, C32 | Polarized Capacitor (Surface Mount) | CapE-6.3-100uF-35V | 100uF 35V | 10 | Approved sub OK | Panasonic Electronic Components (https://octopart-clicks.com/click/altium?manufacturer=Panasonic%20Electronic%20Components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) | EEE-FT1V101AP (https://octopart-clicks.com/click/altium?manufacturer=Panasonic%20Electronic%20Components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) | Digi-Key | PCE5016CT-ND (https://octopart-clicks.com/click/altium?manufacturer=Panasonic%20Electronic%20Components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)
C10 | Capacitor SMD Cer 2.7nF 10% 50V X7R 0603 | CapC-0603-2.7nF | 2.7nF | 1 | Approved sub OK | Yageo (https://octopart-clicks.com/click/altium?sku=311-1344-1-ND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) | CC0603KRX7R9BB104 (https://octopart-clicks.com/click/altium?sku=311-1344-1-ND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) | Digi-Key | 311-1344-1-ND (https://octopart-clicks.com/click/altium?sku=311-1344-1-ND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)
C17 | Capacitor SMD Cer 4.7uF 10% 50V X7R 1210 | CapC-1210-4.7uF-50V | 4.7uF | 1 | Approved sub OK | Murata Electronics North America (https://octopart-clicks.com/click/altium?sku=490-1864-1-ND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) | GRM32ER71H475KA88L (https://octopart-clicks.com/click/altium?sku=490-1864-1-ND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) | Digi-Key | 490-1864-1-ND (https://octopart-clicks.com/click/altium?sku=490-1864-1-ND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)
C3, C9, C12, C26, C27, C28, C29 | Capacitor SMD Cer 1uF 10% 50V X7R 0603 | approved sub OK | 1µ | 7 | Approved sub OK | TDK Corporation (https://octopart-clicks.com/click/altium?sku=445-1604-1-ND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) | C1608X7R1C105K (https://octopart-clicks.com/click/altium?sku=445-1604-1-ND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) | Digi-Key | 445-1604-1-ND (https://octopart-clicks.com/click/altium?sku=445-1604-1-ND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)
C4, C5, C6, C7, C11, C13, C16, C18, C33, C34 | Capacitor SMD Cer 100nF 10% 50V X7R 0603 | CapC-0603-100nF | 100nF | 10 | Approved sub OK | Yageo (https://octopart-clicks.com/click/altium?sku=311-1344-1-ND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) | CC0603KRX7R9BB104 (https://octopart-clicks.com/click/altium?sku=311-1344-1-ND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) | Digi-Key | 311-1344-1-ND (https://octopart-clicks.com/click/altium?sku=311-1344-1-ND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)
C8, C14, C15, C19, C20 | Capacitor SMD Cer 22pF 10% 50V X7R 0603 | CapC-0603-22pF | 22pF | 5 | Approved sub OK | AVX Corporation (https://octopart-clicks.com/click/altium?sku=478-6204-1-ND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) | 06035C220JAT2A (https://octopart-clicks.com/click/altium?sku=478-6204-1-ND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) | Digi-Key | 478-6204-1-ND (https://octopart-clicks.com/click/altium?sku=478-6204-1-ND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)
D1, D6, D7, D9, D10, D11, D12, D13, D14 | Diode SMD 100V 1.5A SMA | 100V; 1.5A | Vf = 1.15V @ 1.5A (Max) | 9 | Approved sub OK | Diodes Inc (https://octopart-clicks.com/click/altium?sku=S2BA-FDICT-ND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) | S2BA-13-F (https://octopart-clicks.com/click/altium?sku=S2BA-FDICT-ND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) | Digi-Key | S2BA-FDICT-ND (https://octopart-clicks.com/click/altium?sku=S2BA-FDICT-ND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)
D2, D3 | Diode SMD 300mA 0.5W SOD323 | DIODE_75V_500mW | Vf=1V @ 50mA | 2 | Approved sub OK | Micro Commercial Co (https://octopart-clicks.com/click/altium?manufacturer=Micro%20Commercial%20Co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) | 1N4148WX-TP (https://octopart-clicks.com/click/altium?manufacturer=Micro%20Commercial%20Co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) | Digi-Key | 1N4148WXTPMSCT-ND (https://octopart-clicks.com/click/altium?manufacturer=Micro%20Commercial%20Co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)
D4 | Schottky Diode | Diode Schottky 2A 20V Dual Common Cathode | PMEG2020CPA,115 | 1 | Approved sub OK | Nexperia USA Inc. (https://octopart-clicks.com/click/altium?manufacturer=Nexperia%20USA%20Inc.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) | PMEG2020CPA,115 (https://octopart-clicks.com/click/altium?manufacturer=Nexperia%20USA%20Inc.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) | Digi-Key | 1727-5194-1-ND (https://octopart-clicks.com/click/altium?manufacturer=Nexperia%20USA%20Inc.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)
D5 | Schottky Diode | Diode Schottky 2A 40V |  | 1 | Approved sub OK | Panasonic Electronic Components (https://octopart-clicks.com/click/altium?manufacturer=Panasonic%20Electronic%20Components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) | DB2W40200L (https://octopart-clicks.com/click/altium?manufacturer=Panasonic%20Electronic%20Components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) | Digi-Key | DB2W40200LCT-ND (https://octopart-clicks.com/click/altium?manufacturer=Panasonic%20Electronic%20Components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)
D8 | Schottky Diode | Diode SSB44-E3 | 40V 4A | 1 | Approved sub OK | Vishay Semiconductor (https://octopart-clicks.com/click/altium?sku=1655-1602-1-ND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) | SSB44-E4/52T (https://octopart-clicks.com/click/altium?sku=1655-1602-1-ND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) | Digi-Key | SSB44-E3/52TGICT-ND (https://octopart-clicks.com/click/altium?sku=1655-1602-1-ND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)
E0_1, E0_2, E1_1, E1_2, E2_1, E2_2, X_1, X_2, Y_1, Y_2, Z_1, Z_2 | Header, 8-Pin Female | Header, 8-Pin Female |  | 12 | Approved sub OK | Generic Header (https://octopart-clicks.com/click/altium?manufacturer=Sullins%20Connector%20Solutions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)
E0_MOT, E1_MOT, E2_MOT, X_MOT, Y_MOT, Z_MOT | Screw Terminal 3.5mm 4-Way | ScrewTerminal-3.5mm-4Way |  | 6 | Approved sub OK | Phoenix Contact (https://octopart-clicks.com/click/altium?sku=277-5744-ND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) | 1751264 (https://octopart-clicks.com/click/altium?sku=277-5744-ND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) | Digi-Key | 277-5744-ND (https://octopart-clicks.com/click/altium?sku=277-5744-ND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)
E0_MOT_A, E1_MOT_A, E2_MOT_A, X_MOT_A, Y_MOT_A, Z_MOT_A, ENC_1, ENC_2, ENC_3, ENC_4 | Header, 4-Pin | Header 4 |  | 10 | Approved sub OK | Generic Header (https://octopart-clicks.com/click/altium?sku=3M9449-ND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)
E0_MS, E1_MS, E2_MS, X_MS, Y_MS, Z_MS | DIP Switch | SW DIP-3 |  | 6 | Approved sub OK | Wurth Electronics Inc. (https://octopart-clicks.com/click/altium?manufacturer=Wurth%20Electronics%20Inc.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) | 416131160803 (https://octopart-clicks.com/click/altium?manufacturer=Wurth%20Electronics%20Inc.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) | Digi-Key | 732-3853-1-ND (https://octopart-clicks.com/click/altium?manufacturer=Wurth%20Electronics%20Inc.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)
EXP1, EXP2, JTAG, Thermistors | Header, 5-Pin, Dual row | Header 5X2 |  | 4 | Approved sub OK | Generic Header (https://octopart-clicks.com/click/altium?sku=3M9460-ND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)
EXP3 | Header, 7-Pin, Dual row | Header 7X2 |  | 1 | Approved sub OK | Generic Header (https://octopart-clicks.com/click/altium?sku=3M15450-ND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)
F1, F2 | Fuseholder - Mini ATC ATO 15A |  |  | 2 | Approved sub OK | MPD (Memory Protection Devices) (https://octopart-clicks.com/click/altium?sku=BK-6013-ND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) | BK-6013 (https://octopart-clicks.com/click/altium?sku=BK-6013-ND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) | Digi-Key | BK-6013-ND (https://octopart-clicks.com/click/altium?sku=BK-6013-ND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)
F3 | Fuse - 15V 200mA Trip PTC SMD 0603 | PTC Resettable Fuse | 200mA | 1 | Approved sub OK | Holly Fuse (https://octopart-clicks.com/click/altium?sku=507-1821-1-ND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) | 06T-0160L (https://octopart-clicks.com/click/altium?sku=507-1821-1-ND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) | Digi-Key | 507-1821-1-ND (https://octopart-clicks.com/click/altium?sku=507-1821-1-ND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)
FAN0, FAN1, HE0, HE1, HE2 | Screw Terminal 3.5mm 2-Way | Screw Terminal 3.5mm 2-Way |  | 5 | Approved sub OK | Phoenix Contact (https://octopart-clicks.com/click/altium?sku=277-5719-ND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) | 1751248 (https://octopart-clicks.com/click/altium?sku=277-5719-ND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) | Digi-Key | 277-5719-ND (https://octopart-clicks.com/click/altium?sku=277-5719-ND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)
HB-OUT, HB-PWR, MAIN-PWR | Screw Terminal 5mm 2-Way | Rising Cage Clamp |  | 3 |  | TE Connectivity AMP Connectors | 282856-2 | Digi-Key | A98355-ND
ISP1, ISP2 | Header, 3-Pin, Dual row | Header 3X2 |  | 2 | Approved sub OK | Generic Header (https://octopart-clicks.com/click/altium?sku=3M9459-ND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)
J2 | Micro-USB B Socket |  |  | 1 | Approved sub OK | Molex, LLC (https://octopart-clicks.com/click/altium?sku=WM1399CT-ND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) | 1050170001 (https://octopart-clicks.com/click/altium?sku=WM1399CT-ND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) | Digi-Key | WM1399CT-ND (https://octopart-clicks.com/click/altium?sku=WM1399CT-ND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)
L1 | Ferrite Bead Inductor | Ferrite Bead SMD 0805 | WE-CBF_0805 (WE-CBF) | 1 | Approved sub OK | Murata Electronics North America (https://octopart-clicks.com/click/altium?sku=490-1054-1-ND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) | BLM21PG221SN1D (https://octopart-clicks.com/click/altium?sku=490-1054-1-ND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) | Digi-Key | 490-1054-1-ND (https://octopart-clicks.com/click/altium?sku=490-1054-1-ND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)
L3 | MagneticCore Inductor with Winding Polarity Marking | Inductor SMD 33uH 2.5A | 33uH | 1 | Approved sub OK | Bourns Inc. (https://octopart-clicks.com/click/altium?sku=SRN6045TA-330MCT-ND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) | SRN6045TA-330M (https://octopart-clicks.com/click/altium?sku=SRN6045TA-330MCT-ND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) | Digi-Key | SRN6045TA-330MCT-ND (https://octopart-clicks.com/click/altium?sku=SRN6045TA-330MCT-ND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)
L4 | MagneticCore Inductor with Winding Polarity Marking | Inductor SMD 47uH 2.2A | 47uH | 1 | Approved sub OK | Bourns Inc. (https://octopart-clicks.com/click/altium?sku=SRN8040TA-470MCT-ND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) | SRN8040TA-470M (https://octopart-clicks.com/click/altium?sku=SRN8040TA-470MCT-ND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) | Digi-Key | SRN8040TA-470MCT-ND (https://octopart-clicks.com/click/altium?sku=SRN8040TA-470MCT-ND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)
LD1, LD2, LD3, LD4, LD5, LD6, LD7, LD8, LD9, LD10 | Hyper-Bright LED | GREEN |  | 10 | Approved sub OK | Lite-On Inc. (https://octopart-clicks.com/click/altium?sku=160-1435-2-ND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) | LTST-C190KGKT (https://octopart-clicks.com/click/altium?sku=160-1435-2-ND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) | Digi-Key | 160-1435-2-ND (https://octopart-clicks.com/click/altium?sku=160-1435-2-ND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)
LED1, RX, TX | Hyper-Bright LED | YELLOW |  | 3 | Approved sub OK | Lite-On Inc. (https://octopart-clicks.com/click/altium?sku=160-1437-1-ND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) | LTST-C190KSKT (https://octopart-clicks.com/click/altium?sku=160-1437-1-ND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) | Digi-Key | 160-1437-1-ND (https://octopart-clicks.com/click/altium?sku=160-1437-1-ND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)
Q1, Q2, Q3, Q4, Q5 | Logic Level N MOSFET | BUK9Y21-40E |  | 5 |  | NXP Semiconductors | BUK9Y21-40E,115 | Digi-Key | 1727-1123-1-ND
Q6 | Logic Level N MOSFET | PSMN1R8-40YLC |  | 1 |  | NXP Semiconductors (https://octopart-clicks.com/click/altium?manufacturer=NXP%20Semiconductors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) | PSMN1R8-40YLC,115 (https://octopart-clicks.com/click/altium?manufacturer=NXP%20Semiconductors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) | Digi-Key | 1727-1052-1-ND
R1, R9 | Resistor | Res-0603-1M | 1M | 2 | Approved sub OK | Yageo (https://octopart-clicks.com/click/altium?sku=311-1.00MHRDKR-ND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) | RC0603FR-071ML (https://octopart-clicks.com/click/altium?sku=311-1.00MHRDKR-ND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) | Digi-Key | 311-1.00MHRDKR-ND (https://octopart-clicks.com/click/altium?sku=311-1.00MHRDKR-ND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)
R10, R22, R24, R26, R28, R30, R32, R35, R38, R44, R47, R49, R52 | Resistor | Res-0603-100K | 100K | 13 | Approved sub OK | Yageo (https://octopart-clicks.com/click/altium?sku=311-100KHRCT-ND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) | RC0603FR-07100KL (https://octopart-clicks.com/click/altium?sku=311-100KHRCT-ND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) | Digi-Key | 311-100KHRCT-ND (https://octopart-clicks.com/click/altium?sku=311-100KHRCT-ND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)
R19 | Resistor | Res-0603-348K | 348K | 1 | Approved sub OK | Yageo (https://octopart-clicks.com/click/altium?sku=311-53.6KHRCT-ND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) | RC0603FR-0753K6L (https://octopart-clicks.com/click/altium?sku=311-53.6KHRCT-ND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) | Digi-Key | 311-53.6KHRCT-ND (https://octopart-clicks.com/click/altium?sku=311-53.6KHRCT-ND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)
R2, R3, R6, R11, R12, R21, R23, R25, R27, R29, R45, R57 | Resistor | Res-0603-10K | 10K | 12 | Approved sub OK | Yageo (https://octopart-clicks.com/click/altium?sku=311-10.0KHRCT-ND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) | RC0603FR-0710KL (https://octopart-clicks.com/click/altium?sku=311-10.0KHRCT-ND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) | Digi-Key | 311-10.0KHRCT-ND (https://octopart-clicks.com/click/altium?sku=311-10.0KHRCT-ND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)
R4, R13, R14, R15, R16, R17, R18, R20, R33, R36, R39, R50, R53, R55, R58 | Resistor | Res-0603-1K | 1K | 15 | Approved sub OK | Yageo (https://octopart-clicks.com/click/altium?sku=311-1.00KHRCT-ND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) | RC0603FR-071KL (https://octopart-clicks.com/click/altium?sku=311-1.00KHRCT-ND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) | Digi-Key | 311-1.00KHRCT-ND (https://octopart-clicks.com/click/altium?sku=311-1.00KHRCT-ND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)
R40, R41, R42, R43, R54, R59 | Resistor | Res-0603-4K7 | 4.7K | 6 | Approved sub OK | Yageo (https://octopart-clicks.com/click/altium?sku=311-4.7KGRCT-ND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) | RC0603JR-074K7L (https://octopart-clicks.com/click/altium?sku=311-4.7KGRCT-ND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) | Digi-Key | 311-4.7KGRCT-ND (https://octopart-clicks.com/click/altium?sku=311-4.7KGRCT-ND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)
R5 | Resistor | Res-0603-54K9 | 54.9k | 1 | Approved sub OK | Yageo (https://octopart-clicks.com/click/altium?sku=311-10.0KHRCT-ND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) | RC0603FR-0710KL (https://octopart-clicks.com/click/altium?sku=311-10.0KHRCT-ND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) | Digi-Key | 311-10.0KHRCT-ND (https://octopart-clicks.com/click/altium?sku=311-10.0KHRCT-ND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)
R56 | Resistor | Res-0603-140K | 140K | 1 | Approved sub OK | Yageo (https://octopart-clicks.com/click/altium?sku=311-1.00KHRCT-ND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) | RC0603FR-071KL (https://octopart-clicks.com/click/altium?sku=311-1.00KHRCT-ND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) | Digi-Key | 311-1.00KHRCT-ND (https://octopart-clicks.com/click/altium?sku=311-1.00KHRCT-ND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)
R7, R8, R31, R34, R37, R46, R48, R51 | Resistor | Res-0603-22R | 22R | 8 | Approved sub OK | Yageo (https://octopart-clicks.com/click/altium?sku=311-22.0HRCT-ND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) | RC0603FR-0722RL (https://octopart-clicks.com/click/altium?sku=311-22.0HRCT-ND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) | Digi-Key | 311-22.0HRCT-ND (https://octopart-clicks.com/click/altium?sku=311-22.0HRCT-ND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)
Reset | SMD Tactile Switch | SW-PB |  | 1 | Approved sub OK | APEM Inc. (https://octopart-clicks.com/click/altium?sku=679-2396-1-ND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) | MJTP1106SATR (https://octopart-clicks.com/click/altium?sku=679-2396-1-ND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) | Digi-Key | 679-2396-1-ND (https://octopart-clicks.com/click/altium?sku=679-2396-1-ND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)
U1 | The high-performance, low-power Atmel 8-bit AVR RISC-based microcontroller | ATMEGA2560 |  | 1 |  | Microchip Technology (https://octopart-clicks.com/click/altium?manufacturer=Microchip%20Technology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) | ATMEGA2560-16AU (https://octopart-clicks.com/click/altium?manufacturer=Microchip%20Technology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) | Digi-Key | ATMEGA2560-16AU-ND (https://octopart-clicks.com/click/altium?manufacturer=Microchip%20Technology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)
U2 | High Performance, Low Power USB2.0 AVR® 8-Bit Microcontroller | ATMEGA16U2-AU |  | 1 |  | Microchip Technology (https://octopart-clicks.com/click/altium?manufacturer=Microchip%20Technology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) | ATMEGA16U2-AU (https://octopart-clicks.com/click/altium?manufacturer=Microchip%20Technology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) | Digi-Key | ATMEGA16U2-AU-ND (https://octopart-clicks.com/click/altium?manufacturer=Microchip%20Technology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)
U3 | Buck Regulator | AOZ1282CI |  | 1 |  | Alpha & Omega Semiconductor Inc. (https://octopart-clicks.com/click/altium?sku=785-1613-1-ND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) | AOZ1282CI (https://octopart-clicks.com/click/altium?sku=785-1613-1-ND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) | Digi-Key | 785-1613-1-ND (https://octopart-clicks.com/click/altium?sku=785-1613-1-ND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)
U4 | Buck Regulator | AOZ1284 |  | 1 |  | Alpha & Omega Semiconductor Inc. (https://octopart-clicks.com/click/altium?sku=785-1689-1-ND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) | AOZ1284PI (https://octopart-clicks.com/click/altium?sku=785-1689-1-ND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) | Digi-Key | 785-1689-1-ND (https://octopart-clicks.com/click/altium?sku=785-1689-1-ND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)
U5 | ESD Protection IC | USBLC6-4SC6 |  | 1 | Approved sub OK | STMicroelectronics (https://octopart-clicks.com/click/altium?sku=497-4492-1-ND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) | USBLC6-4SC6 (https://octopart-clicks.com/click/altium?sku=497-4492-1-ND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) | Digi-Key | 497-4492-1-ND (https://octopart-clicks.com/click/altium?sku=497-4492-1-ND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)
USB_AUX | Header, 5-Pin | Header 5 |  | 1 | Approved sub OK | Generic Header (https://octopart-clicks.com/click/altium?sku=3M9449-ND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)
VFA0_sel, VFA1_sel, VHE2_sel, X+, X-, Y+, Y-, Z+, Z- | Header, 3-Pin | Header 3 |  | 9 | Approved sub OK | Generic Header (https://octopart-clicks.com/click/altium?sku=3M9448-ND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)
Y1, Y2 | Crystal Oscillator | 16MHz |  | 2 | Approved sub OK | EPSON (https://octopart-clicks.com/click/altium?sku=SER3686CT-ND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) | FA-238 16.0000MB-C3 (https://octopart-clicks.com/click/altium?sku=SER3686CT-ND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) | Digi-Key | SER3686CT-ND (https://octopart-clicks.com/click/altium?sku=SER3686CT-ND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)

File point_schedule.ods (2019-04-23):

name | IO DIRECTION | # | TERMINALS
MOTOR – X AXIS
DIR | OUTPUT | 1 | 1
STEP | OUTPUT | 1 | 1
ENABLE | OUTPUT | 1 | 1
END STOP | INPUT | 1 | 1
MOTOR – Y AXIS
DIR | OUTPUT | 1 | 1
STEP | OUTPUT | 1 | 1
ENABLE | OUTPUT | 1 | 1
END STOP | INPUT | 1 | 1
MOTOR – Z (0,1,2,3)
DIR | OUTPUT | 4 | 4
STEP | OUTPUT | 4 | 4
ENABLE | OUTPUT | 4 | 4
END STOP | INPUT | 4 | 4
PROBE | INPUT | 1 | 1
MOTOR – E(0,1,2,3)
DIR | OUTPUT | 4 | 4
STEP | OUTPUT | 4 | 4
ENABLE | OUTPUT | 4 | 4
HOTEND HEATER | OUTPUT | 4 | 4
HOTEND TEMPERATURE | OUTPUT | 4 | 4
FAN
FAN1, HOTEND FAN | OUTPUT | 1 | 1
FAN2, CONTROLLER FAN | OUTPUT | 1 | 1
FAN3, EXHAUST FAN | OUTPUT | 1 | 1
FAN4 | OUTPUT | 1 | 1
FAN5 | OUTPUT | 1 | 1
HEATBED
HEATBED | OUTPUT | 1 | 1
DEBUG (STM32 SOLUTION)
SWD
LED – PC13

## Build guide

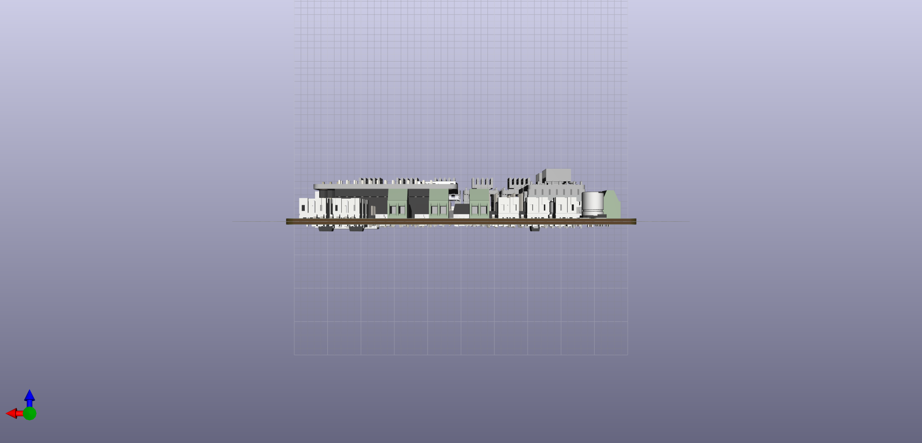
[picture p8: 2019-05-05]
hardware/printer-board/renders/Y_printer-board.png

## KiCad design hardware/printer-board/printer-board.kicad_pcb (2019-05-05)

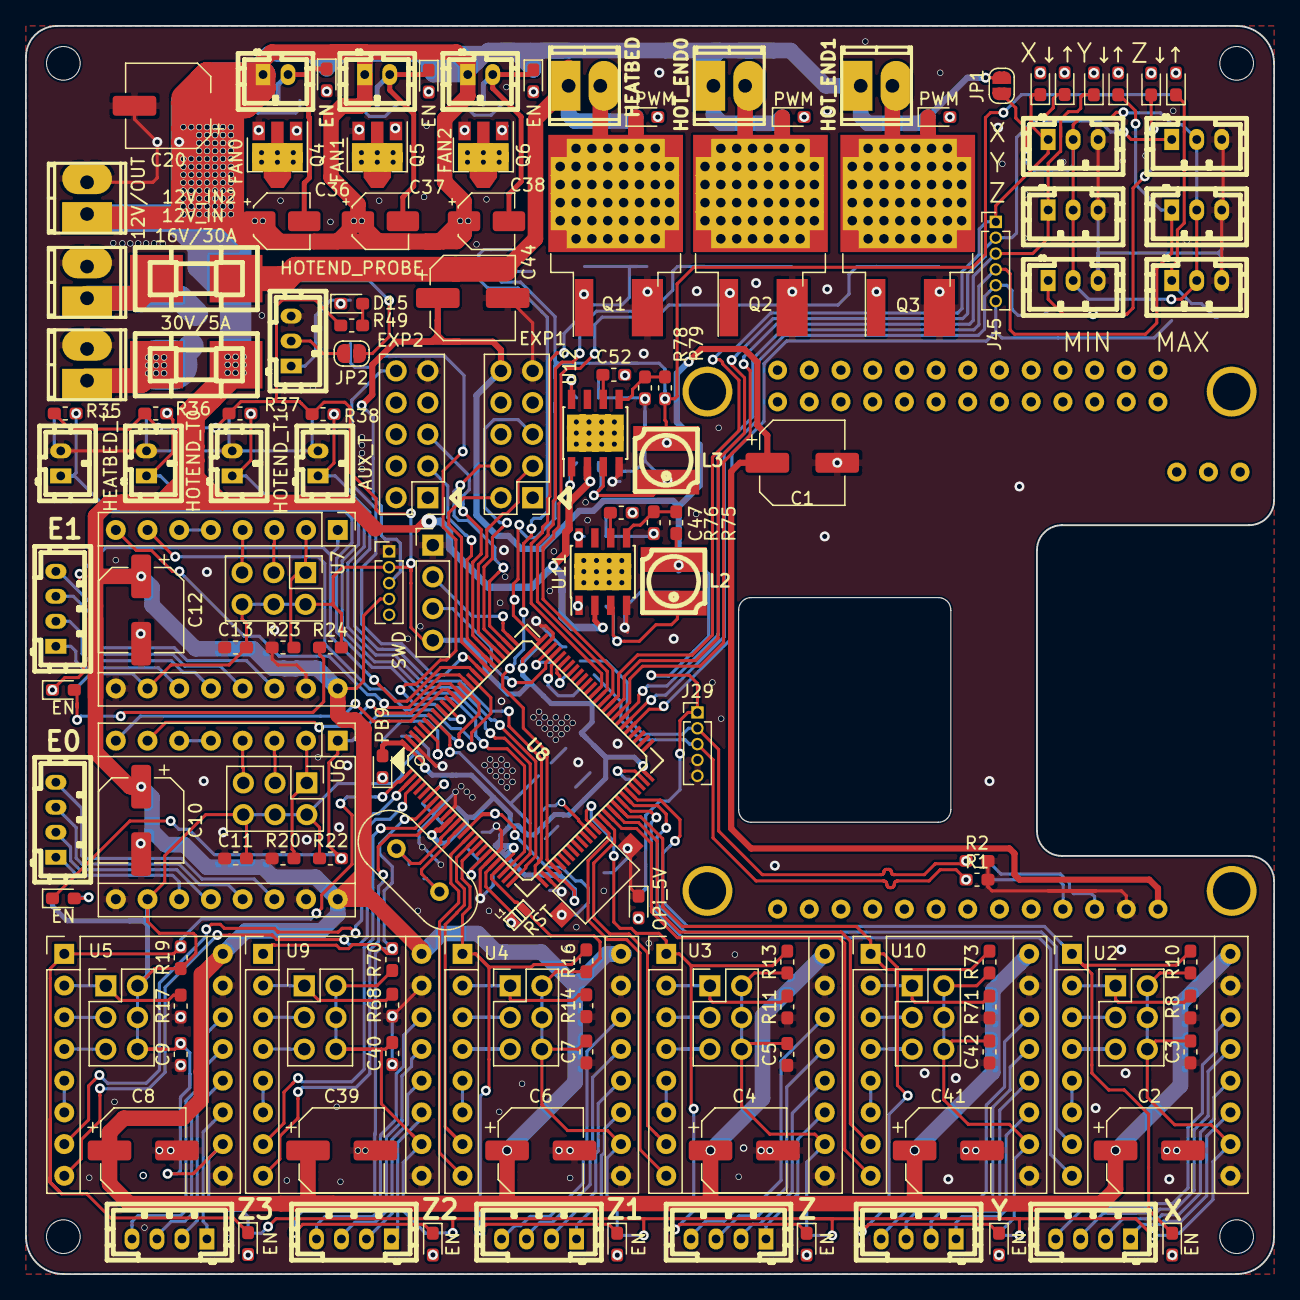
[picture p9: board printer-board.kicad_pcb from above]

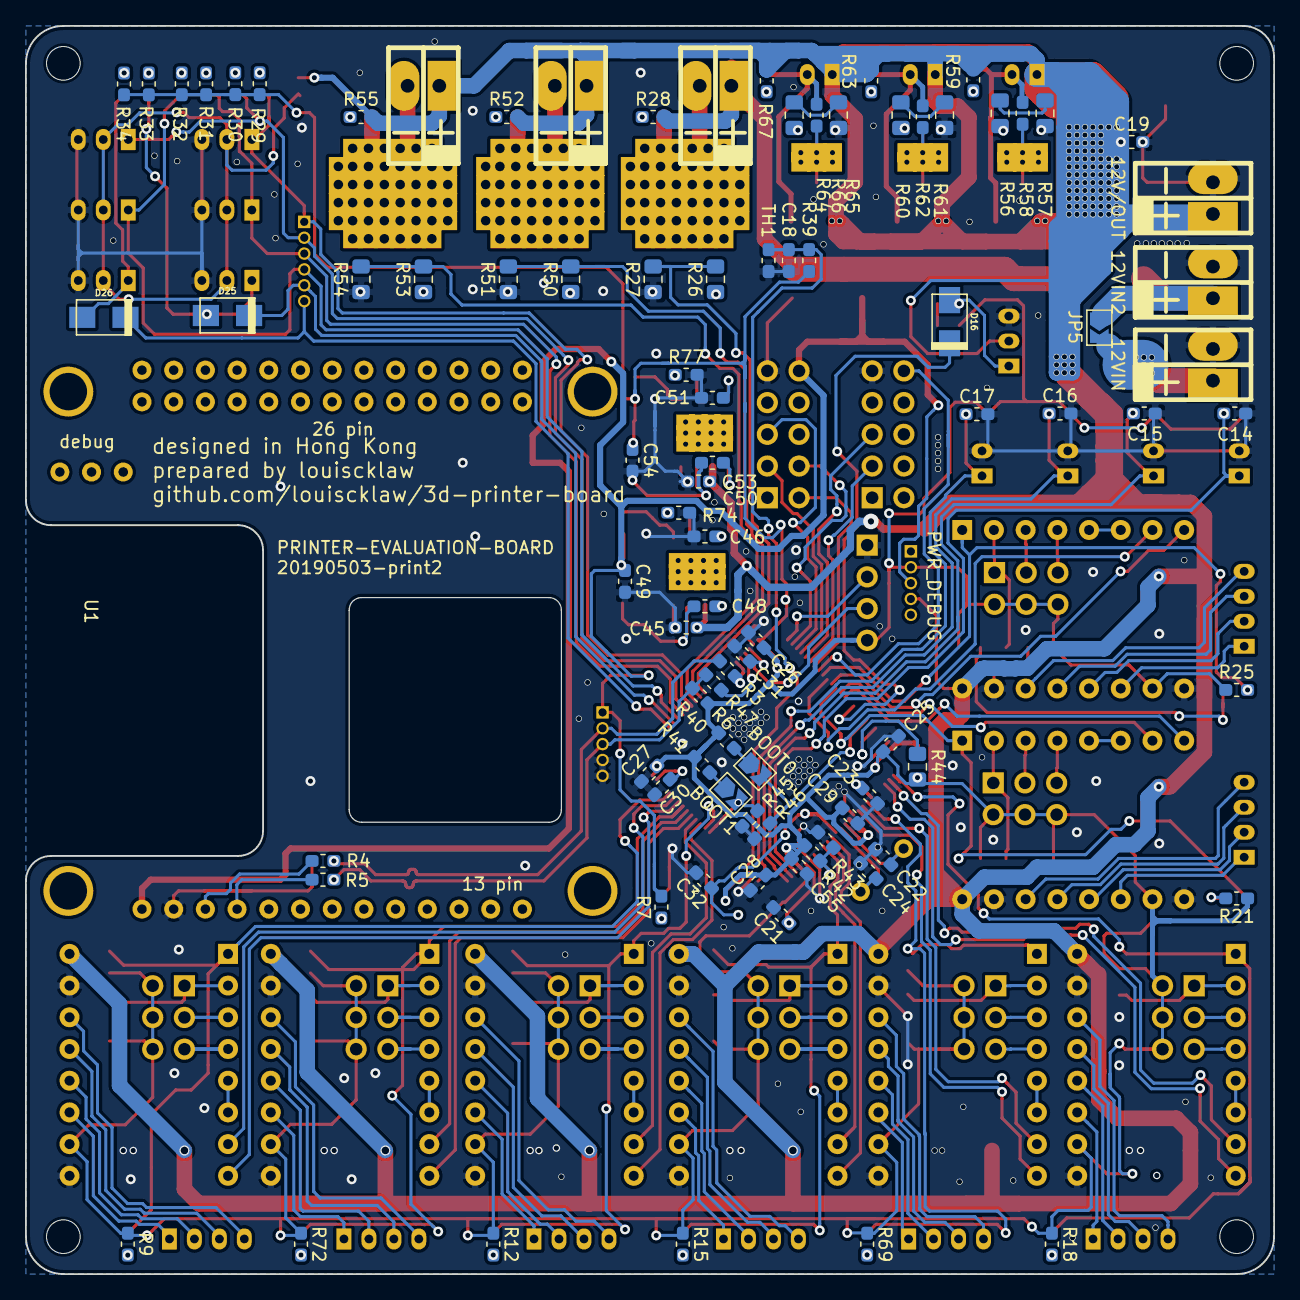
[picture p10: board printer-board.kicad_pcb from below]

Board: 2 copper layers, 100.0 x 100.0 mm, 232 parts (86 on the bottom side), 194 nets.

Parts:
C1: CP100uf,10V; CP_Elec_6.3x5.3
C2, C4, C6, C8, C10, C12, C39, C41: CP100uf,25V; CP_Elec_6.3x7.7
C3, C5, C7, C9, C11, C13, C19, C21, C23, C25, C26, C27, C28, C30, C31, C32, C40, C42, C46, C51: C104,0603; C_0603_1608Metric_Pad1.05x0.95mm_HandSolder
C14, C15, C16, C17, C18, C45, C50: C106,0603; C_0603_1608Metric_Pad1.05x0.95mm_HandSolder
C20: CP100uf,35V; CP_Elec_6.3x7.7
C22, C24: C10pf,0603; C_0603_1608Metric_Pad1.05x0.95mm_HandSolder
C29, C55: C105,0603; C_0603_1608Metric_Pad1.05x0.95mm_HandSolder
C36, C37, C38: CP1uf,50V; CP_Elec_4x5.3
C44: CP100uf,16V; CP_Elec_6.3x5.3
C47, C52: C332,0603; C_0603_1608Metric_Pad1.05x0.95mm_HandSolder
C48, C53: C103,0603; C_0603_1608Metric_Pad1.05x0.95mm_HandSolder
C49, C54: C226,6.3v,0603; C_0603_1608Metric_Pad1.05x0.95mm_HandSolder
D1: OPi_5V; LED_0603_1608Metric_Pad1.05x0.95mm_HandSolder
D2, D3, D4, D5, D6, D7, D20, D21, D22, D23, D24: EN; LED_0603_1608Metric_Pad1.05x0.95mm_HandSolder
D8, D18, D19: PWM; LED_0603_1608Metric_Pad1.05x0.95mm_HandSolder
D9: X↓; LED_0603_1608Metric_Pad1.05x0.95mm_HandSolder
D10, D12, D14: ↑; LED_0603_1608Metric_Pad1.05x0.95mm_HandSolder
D11: Y↓; LED_0603_1608Metric_Pad1.05x0.95mm_HandSolder
D13: Z↓; LED_0603_1608Metric_Pad1.05x0.95mm_HandSolder
D15: LED_BLUE,0603; LED_0603_1608Metric_Pad1.05x0.95mm_HandSolder
D16, D25, D26: SD_1N5817_SS12; do214ac
D17: PB9; LED_0603_1608Metric_Pad1.05x0.95mm_HandSolder
F1: 16V/30A; fuse_smf
F2: 30V/5A; fuse_smf
H1, H2, H3, H4: MOUNT_M3; MountingHole_2.7mm_M2.5
J2, J4, J6, J8, J10, J12, J36, J38: MS_SELECT; PinHeader_2x03_P2.54mm_Vertical
J3: X; b4b-ph-kl,stepper_terminal
J5: Z; b4b-ph-kl,stepper_terminal
J7: Z1; b4b-ph-kl,stepper_terminal
J9: Z3; b4b-ph-kl,stepper_terminal
J11: E0; b4b-ph-kl,stepper_terminal
J13: E1; b4b-ph-kl,stepper_terminal
J14: HEATBED; mpt_0,5%2f2-2,54,heatbed
J15: X_MIN; b3b-ph-kl,end_stop
J16: X_MAX; b3b-ph-kl,end_stop
J17: Y_MIN; b3b-ph-kl,end_stop
J18: Y_MAX; b3b-ph-kl,end_stop
J19: Z_MIN; b3b-ph-kl,end_stop
J20: Z_MAX; b3b-ph-kl,end_stop
J21: HEATBED_T; b2b-ph-kl
J22: HOTEND_T0; b2b-ph-kl
J23: HOTEND_T1; b2b-ph-kl
J24: AUX_T; b2b-ph-kl
J25: 12V_IN2; mpt_0,5%2f2-2,54,12V_SRC
J26: 12V_IN; mpt_0,5%2f2-2,54,12V_SRC
J27: 12V/OUT; mpt_0,5%2f2-2,54,12V_SRC
J28: SWD; PinHeader_1x04_P2.54mm_Vertical
J29: STM32_USB_DEBUG; PinHeader_1x05_P1.27mm_Vertical
J30: PWR_DEBUG; PinHeader_1x05_P1.27mm_Vertical
J31: HOT_END0; mpt_0,5%2f2-2,54,heatbed
J32: HOT_END1; mpt_0,5%2f2-2,54,heatbed
J33: FAN0; b2b-ph-kl,fan_pwm_out
J34: FAN1; b2b-ph-kl,fan_pwm_out
J35: FAN2; b2b-ph-kl,fan_pwm_out
J37: Z2; b4b-ph-kl,stepper_terminal
J39: Y; b4b-ph-kl,stepper_terminal
J41: EXP1; PinHeader_2x05_P2.54mm_Vertical
J42: EXP2; PinHeader_2x05_P2.54mm_Vertical
J45: END_SWITCH_DEBUG; PinHeader_1x06_P1.27mm_Vertical
J48: HOTEND_PROBE; b3b-ph-kl,end_stop
JP1, JP2: SolderJumper_2_Open; SolderJumper-2_P1.3mm_Open_RoundedPad1.0x1.5mm
JP5: Jumper_NO_Small; SolderJumper-2_P1.3mm_Open_TrianglePad1.0x1.5mm
JP6: BOOT0; SolderJumper-2_P1.3mm_Open_TrianglePad1.0x1.5mm
JP7: BOOT1; SolderJumper-2_P1.3mm_Open_TrianglePad1.0x1.5mm
L1: L_Small; inductor_smd_0603
L2, L3: L_15uH; inductor_smd_4.8x2.8mm
Q1: WSK220N04; TO-263-2,thermal_vias
Q2, Q3: STP55NF06; TO-263-2,thermal_vias
Q4, Q5, Q6: D882; SOT-89-3,thermal_vias
R1, R2: R153,0603; R_0603_1608Metric_Pad1.05x0.95mm_HandSolder
R3, R4, R5, R47: R220,0603; R_0603_1608Metric_Pad1.05x0.95mm_HandSolder
R6: R152,0603; R_0603_1608Metric_Pad1.05x0.95mm_HandSolder
R7, R9, R12, R15, R18, R21, R24, R29, R30, R31, R32, R33, R34, R49, R69, R72: R102,0603; R_0603_1608Metric_Pad1.05x0.95mm_HandSolder
R8, R11, R14, R17, R20, R23, R68, R71: R104,0603; R_0603_1608Metric_Pad1.05x0.95mm_HandSolder
R10, R13, R16, R19, R22, R25, R45, R46, R70, R73, R75, R78: R103,0603; R_0603_1608Metric_Pad1.05x0.95mm_HandSolder
R26, R50, R53, R56, R60, R64: R100,0805; R_0805_2012Metric_Pad1.15x1.40mm_HandSolder
R27, R51, R54, R57, R61, R65: R104,0805; R_0805_2012Metric_Pad1.15x1.40mm_HandSolder
R28, R52, R55, R59, R63, R67: R182,0603; R_0603_1608Metric_Pad1.05x0.95mm_HandSolder
R35, R36, R37, R38, R39, R40, R41: R472,0603; R_0603_1608Metric_Pad1.05x0.95mm_HandSolder
R42: R0,0603; C_0603_1608Metric_Pad1.05x0.95mm_HandSolder
R43: R0,0603; R_0603_1608Metric_Pad1.05x0.95mm_HandSolder
R44: R102,0603; R_0805_2012Metric_Pad1.15x1.40mm_HandSolder
R58, R62, R66: R100,0603; R_0603_1608Metric_Pad1.05x0.95mm_HandSolder
R74, R77: R562,0603; R_0603_1608Metric_Pad1.05x0.95mm_HandSolder
R76: R183,0603; R_0603_1608Metric_Pad1.05x0.95mm_HandSolder
R79: R333,0603; R_0603_1608Metric_Pad1.05x0.95mm_HandSolder
SW1: RST; SW_SPST_CK_RS282G05A3
TH1: Thermistor_NTC; R_0603_1608Metric_Pad1.05x0.95mm_HandSolder
U1: orange_pi_zero; orangepi-zero
U2, U3, U4, U5, U6, U7, U9, U10: A4988_MODULE; Pololu_Breakout-16_15.2x20.3mm
U8: STM32F407VET6; TQFP-100
U11, U12: MP2303A_ALT; SOIC-8_3.9x4.9mm_P1.27mm,thermal_via
Y1: O_8M; Crystal_HC49-4H_Vertical

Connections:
+3V3: C3.2, C5.2, C7.2, C9.2, C11.2, C13.2, C25.2, C26.2, C27.2, C28.2, C29.2, C40.2, C42.2, C54.1, C55.2, D17.2, J2.2, J2.4, J2.6, J4.2, J4.4, J4.6, J6.2, J6.4, J6.6, J8.2, J8.4, J8.6, J10.2, J10.4, J10.6, J12.2, J12.4, J12.6, J28.4, J30.2, J36.2, J36.4, J36.6, J38.2, J38.4, J38.6, L1.1, L3.2, R6.2, R9.1, R10.1, R12.1, R13.1, R15.1, R16.1, R18.1, R19.1, R21.1, R22.1, R24.1, R25.1, R29.1, R30.1, R31.1, R32.1, R33.1, R34.1, R35.1, R36.1, R37.1, R38.1, R39.1, R40.2, R41.2, R42.2, R49.1, R69.1, R70.1, R72.1, R73.1, R79.1, U2.10, U3.10, U4.10, U5.10, U6.10, U7.10, U8.11, U8.22, U8.28, U8.50, U8.75, U8.100, U9.10, U10.10
+5V: C1.1, C44.1, C49.1, J29.1, J30.3, J41.10, L2.2, R7.2, R76.1, U1.1
+12V: C2.1, C4.1, C6.1, C8.1, C10.1, C12.1, C19.1, C20.1, C36.1, C37.1, C38.1, C39.1, C41.1, C45.1, C50.1, F2.2, J27.1, J30.4, J31.1, J32.1, J33.1, J34.1, J35.1, JP1.1, JP2.1, R52.2, R55.2, R59.2, R63.2, R67.2, U2.16, U3.16, U4.16, U5.16, U6.16, U7.16, U9.16, U10.16, U11.2, U12.2
+12V2: F1.2, J14.1, R28.2
/FANS/FAN0/FAN0_N: C36.2, D20.1, J33.2, R58.1
/FANS/FAN1/FAN1_N: C37.2, D21.1, J34.2, R62.1
/FANS/FAN2/FAN2_N: C38.2, D22.1, J35.2, R66.1
/HEATBED/-12V2: D8.1, J14.2, Q1.2
/HOTENDS/HOTEND_0/-12V: D18.1, J31.2, Q2.2
/HOTENDS/HOTEND_1/-12V: D19.1, J32.2, Q3.2
/STM32_CORE/STM32_CORE_MCU/BOOT0: JP6.2, R46.1, U8.94
/STM32_CORE/STM32_CORE_MCU/BOOT1: JP7.2, R45.1, U8.37
/STM32_CORE/STM32_CORE_MCU/DM: R3.1, U8.70
/STM32_CORE/STM32_CORE_MCU/DP: R47.1, U8.71
/STM32_CORE/STM32_CORE_MCU/GND-CAP1: C30.1, U8.49
/STM32_CORE/STM32_CORE_MCU/GND-CAP2: C31.1, U8.73
/STM32_CORE/STM32_CORE_MCU/GND-VCC3V3: R42.1, R43.1, U8.19
/STM32_CORE/STM32_CORE_MCU/RESET: C32.1, SW1.2, U8.14
/STM32_CORE/STM32_CORE_MCU/SWCLK: J28.2, U8.76
/STM32_CORE/STM32_CORE_MCU/SWDIO: J28.3, U8.72
/orange_pi/OPI_USB-DM2: J29.2, R2.1, R3.2, R4.2
/orange_pi/OPI_USB-DP2: J29.3, R1.1, R5.2, R6.1, R47.2
/orange_pi/USB-DM2: R4.1, U1.3
/orange_pi/USB-DP2: R5.1, U1.4
GND: C1.2, C2.2, C3.1, C4.2, C5.1, C6.2, C7.1, C8.2, C9.1, C10.2, C11.1, C12.2, C13.1, C14.2, C15.2, C16.2, C17.2, C18.2, C19.2, C20.2, C21.2, C22.2, C23.2, C24.2, C25.1, C26.1, C27.1, C28.1, C29.1, C30.2, C31.2, C32.2, C39.2, C40.1, C41.2, C42.1, C44.2, C45.2, C46.2, C49.2, C50.2, C51.2, C54.2, C55.1, D1.1, J15.3, J16.3, J17.3, J18.3, J19.3, J20.3, J21.2, J22.2, J23.2, J24.2, J25.2, J26.2, J27.2, J28.1, J29.4, J29.5, J30.1, J41.9, J42.9, J48.3, Q1.3, Q2.3, Q3.3, Q4.3, Q5.3, Q6.3, R1.2, R2.2, R8.1, R11.1, R14.1, R17.1, R20.1, R23.1, R27.1, R43.2, R45.2, R46.2, R51.1, R54.1, R57.1, R61.1, R65.1, R68.1, R71.1, R74.2, R75.2, R77.2, R78.2, SW1.1, TH1.2, U1.2, U2.9, U2.15, U3.9, U3.15, U4.9, U4.15, U5.9, U5.15, U6.9, U6.15, U7.9, U7.15, U8.10, U8.20, U8.27, U8.74, U8.99, U9.9, U9.15, U10.9, U10.15, U11.4, U12.4
unnamed: C21.1, L1.2, U8.21
unnamed: C22.1, U8.12, Y1.1
unnamed: C23.1, U8.6
unnamed: C24.1, U8.13, Y1.2
unnamed: C46.1, U11.8
unnamed: C47.1, U11.6
unnamed: C47.2, R74.1
unnamed: C48.1, L2.1, U11.3
unnamed: C48.2, U11.1
unnamed: C51.1, U12.8
unnamed: C52.1, U12.6
unnamed: C52.2, R77.1
unnamed: C53.1, L3.1, U12.3
unnamed: C53.2, U12.1
unnamed: D1.2, R7.1
unnamed: D2.2, R9.2
unnamed: D3.2, R12.2
unnamed: D4.2, R15.2
unnamed: D5.2, R18.2
unnamed: D6.2, R21.2
unnamed: D7.2, R24.2
unnamed: D8.2, R28.1
unnamed: D9.2, R29.2
unnamed: D10.2, R30.2
unnamed: D11.2, R31.2
unnamed: D12.2, R32.2
unnamed: D13.1, D25.1, J19.1
unnamed: D13.2, R33.2
unnamed: D14.1, D26.1, J20.1
unnamed: D14.2, R34.2
unnamed: D15.1, D16.1, J48.1
unnamed: D15.2, R49.2
unnamed: D17.1, R44.2
unnamed: D18.2, R52.1
unnamed: D19.2, R55.1
unnamed: D20.2, R59.1
unnamed: D21.2, R63.1
unnamed: D22.2, R67.1
unnamed: D23.2, R69.2
unnamed: D24.2, R72.2
unnamed: F1.1, J25.1, JP5.1
unnamed: F2.1, J26.1, JP5.2
unnamed: J2.1, R8.2, U2.2
unnamed: J2.3, U2.3
unnamed: J2.5, U2.4
unnamed: J3.1, U2.11
unnamed: J3.2, U2.12
unnamed: J3.3, U2.13
unnamed: J3.4, U2.14
unnamed: J4.1, R11.2, U3.2
unnamed: J4.3, U3.3
unnamed: J4.5, U3.4
unnamed: J5.1, U3.11
unnamed: J5.2, U3.12
unnamed: J5.3, U3.13
unnamed: J5.4, U3.14
unnamed: J6.1, R14.2, U4.2
unnamed: J6.3, U4.3
unnamed: J6.5, U4.4
unnamed: J7.1, U4.11
unnamed: J7.2, U4.12
unnamed: J7.3, U4.13
unnamed: J7.4, U4.14
unnamed: J8.1, R17.2, U5.2
unnamed: J8.3, U5.3
unnamed: J8.5, U5.4
unnamed: J9.1, U5.11
unnamed: J9.2, U5.12
unnamed: J9.3, U5.13
unnamed: J9.4, U5.14
unnamed: J10.1, R20.2, U6.2
unnamed: J10.3, U6.3
unnamed: J10.5, U6.4
unnamed: J11.1, U6.11
unnamed: J11.2, U6.12
unnamed: J11.3, U6.13
unnamed: J11.4, U6.14
unnamed: J12.1, R23.2, U7.2
unnamed: J12.3, U7.3
unnamed: J12.5, U7.4
unnamed: J13.1, U7.11
unnamed: J13.2, U7.12
unnamed: J13.3, U7.13
unnamed: J13.4, U7.14
unnamed: J15.2, J16.2, J17.2, J18.2, J19.2, J20.2, JP1.2
unnamed: J36.1, R68.2, U9.2
unnamed: J36.3, U9.3
unnamed: J36.5, U9.4
unnamed: J37.1, U9.11
unnamed: J37.2, U9.12
unnamed: J37.3, U9.13
unnamed: J37.4, U9.14
unnamed: J38.1, R71.2, U10.2
unnamed: J39.1, U10.11
unnamed: J39.2, U10.12
unnamed: J39.3, U10.13
unnamed: J39.4, U10.14
unnamed: J48.2, JP2.2
unnamed: JP6.1, R40.1
unnamed: JP7.1, R41.1
unnamed: Q1.1, R26.1
unnamed: Q2.1, R50.1
unnamed: Q3.1, R53.1
unnamed: Q4.1, R56.1
unnamed: Q4.2, R58.2
unnamed: Q5.1, R60.1
unnamed: Q5.2, R62.2
unnamed: Q6.1, R64.1
unnamed: Q6.2, R66.2
unnamed: R75.1, R76.2, U11.5
unnamed: R78.1, R79.2, U12.5
unnamed: U2.5, U2.6
unnamed: U3.5, U3.6
unnamed: U4.5, U4.6
unnamed: U5.5, U5.6
unnamed: U6.5, U6.6
unnamed: U7.5, U7.6
unnamed: U9.5, U9.6
unnamed: U10.5, U10.6
PA0: C14.1, J21.1, R35.2, U8.23
PA1: C15.1, J22.1, R36.2, U8.24
PA2: C16.1, J23.1, R37.2, U8.25
PA3: C17.1, J24.1, R38.2, U8.26
PA4: C18.1, R39.2, TH1.1, U8.29
PA11: R56.2, R57.2
PA12: R60.2, R61.2
PA13: R64.2, R65.2
PA15: J41.4, U8.77
PB3: U6.8, U8.89
PB5: D16.2, U8.91
PB9: R44.1, U8.96
PC0: U4.8, U8.15
PC1: U4.7, U8.16
PC2: D4.1, R16.2, U4.1, U8.17
PC6: R26.2, R27.2, U8.63
PC10: J41.5, U8.78
PC11: J41.3, U8.79
PC12: J42.5, U8.80
PC13: D23.1, R70.2, U8.7, U9.1
PC14: U8.8, U9.7
PC15: U8.9, U9.8
PD0: J42.3, U8.81
PD1: J41.2, U8.82
PD2: J42.10, U8.83
PD3: D7.1, R25.2, U7.1, U8.84
PD4: U7.7, U8.85
PD5: U7.8, U8.86
PD6: D6.1, R22.2, U6.1, U8.87
PD7: U6.7, U8.88
PD8: D26.2, J45.6, U8.55
PD9: D25.2, J45.5, U8.56
PD10: D12.1, J18.1, J45.4, U8.57
PD11: D11.1, J17.1, J45.3, U8.58
PD12: D10.1, J16.1, J45.2, U8.59
PD13: D9.1, J15.1, J45.1, U8.60
PD14: R53.2, R54.2, U8.61
PD15: R50.2, R51.2, U8.62
PE2: D5.1, R19.2, U5.1, U8.1
PE3: U5.7, U8.2
PE4: U5.8, U8.3
PE7: D3.1, R13.2, U3.1, U8.38
PE8: U3.8, U8.39
PE9: U3.7, U8.40
PE10: U8.41, U10.8
PE11: U8.42, U10.7
PE12: D24.1, R73.2, U8.43, U10.1
PE13: U2.8, U8.44
PE14: U2.7, U8.45
PE15: D2.1, R10.2, U2.1, U8.46

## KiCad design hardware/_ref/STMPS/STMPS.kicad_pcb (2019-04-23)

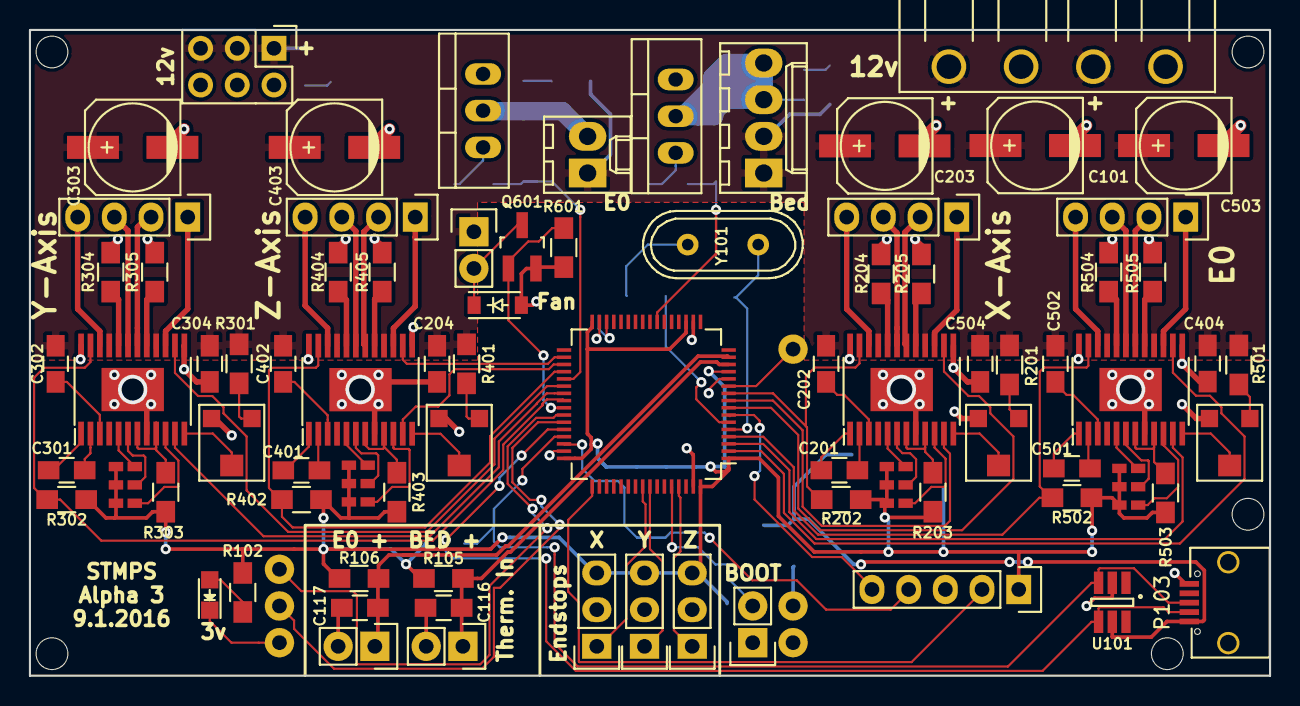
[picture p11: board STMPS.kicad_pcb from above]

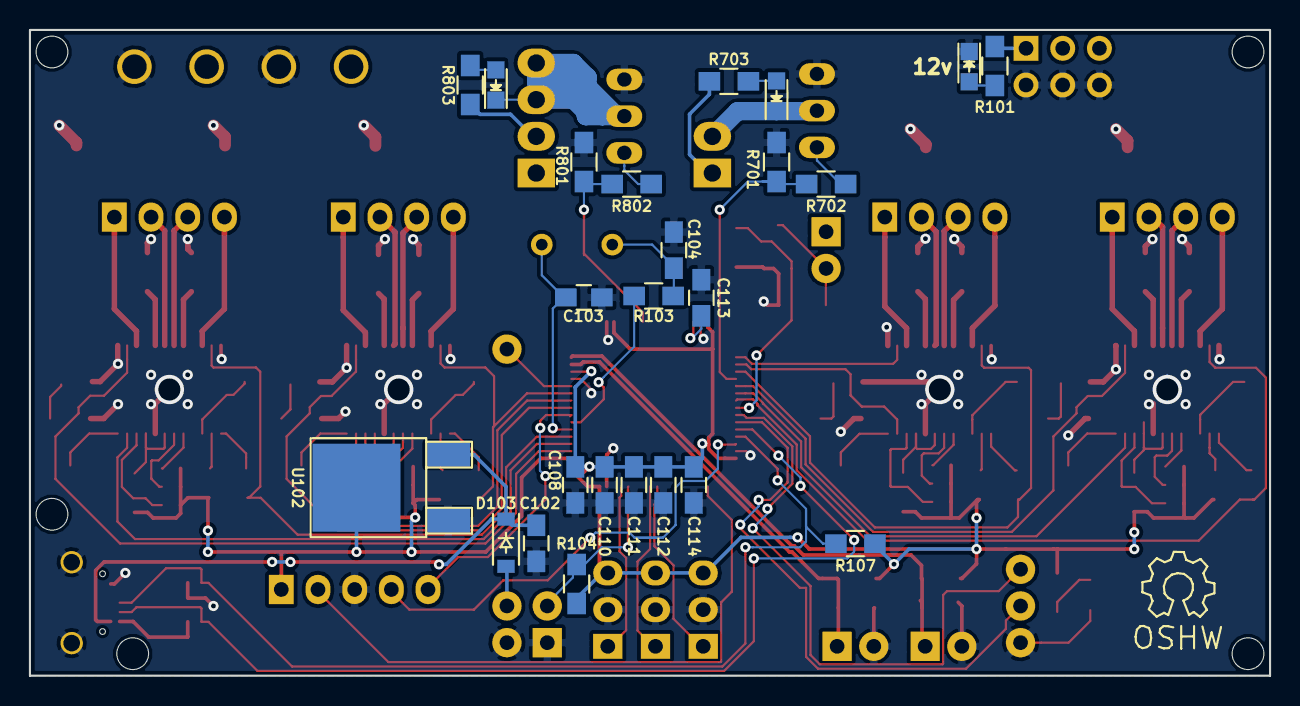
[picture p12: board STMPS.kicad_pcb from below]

Board: 2 copper layers, 85.9 x 44.7 mm, 113 parts (24 on the bottom side), 107 nets.

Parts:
C101, C203, C303, C403, C503: 100uf; c_elec_6.3x5.8
C102, C116, C117: 10uf; C_0805_HandSoldering
C103, C104: 20pf; C_0805_HandSoldering
C108, C110, C111, C112: 100nf; C_0805_HandSoldering
C113, C114: 4.7uf; C_0805_HandSoldering
C201, C202, C204, C301, C302, C304, C401, C402, C404, C501, C502, C504: 0.1uf; C_0805_HandSoldering
D101: 12v_PWR; LED_0805
D102: 3v_PWR; LED_0805
D103, D601: D_Schottky_Small; SOD-123
D701, D801: r; LED_0805
JP101: BOOT0; Pin_Header_Straight_1x02
JP201, JP301, JP401, JP501: MS3; MADW__SMD-solder-bridge-narrow
JP202, JP302, JP402, JP502: MS2; MADW__SMD-solder-bridge-narrow
JP203, JP303, JP403, JP503: MS1; MADW__SMD-solder-bridge-narrow
P101: 12v IN; 5EHDRC_1x04
P102: 12v; Pin_Header_Straight_2x03
P103: USB_OTG; USB_Micro-B-ebay
P104: E0_THERM; Pin_Header_Straight_1x02
P105: X_STOP; Pin_Header_Straight_1x03
P106: SWD; Pin_Header_Straight_1x05
P107: BED_THERM; Pin_Header_Straight_1x02
P108: Y_STOP; Pin_Header_Straight_1x03
P109: Z_STOP; Pin_Header_Straight_1x03
P110: BED; Molex_KK-6410-04_04x2.54mm_Straight
P111: EO; Molex_KK-6410-02_02x2.54mm_Straight
P201, P301, P401, P501: MOT; Pin_Header_Straight_1x04
P601: LP_OUT; Pin_Header_Straight_1x02
Q601: SSM3K333; SOT-23_Handsoldering
Q701, Q801: IPP039N04L; TO-220_Neutral123_Vertical
R101, R703, R803: 560; R_0805_HandSoldering
R102: 56; R_0805_HandSoldering
R103: 220; R_0805_HandSoldering
R104, R202, R203, R302, R303, R402, R403, R502, R503, R601, R701, R801: 100k; R_0805_HandSoldering
R105, R106, R107: 4.7k; R_0805_HandSoldering
R201, R301, R401, R501: 200k; R_0805_HandSoldering
R204, R205, R304, R305, R404, R405, R504, R505: 0.1; R_0805_HandSoldering
R702, R802: 100; R_0805_HandSoldering
RV201, RV301, RV401, RV501: 100k; BOURNS-TC33X-2
U101: AOZ8904; SOT-23-6_Handsoldering
U102: LM1117-3.3v; TO-252-2Lead
U103: STM32F411RCTx; LQFP-64_10x10mm_Pitch0.5mm
U105: CHIP-TOP; CHIP-MIN
U201, U301, U401, U501: A5984; TSSOP-24_4.4x7.8mm_Pitch0.65mm
Y101: Crystal; Crystal_HC49-U_Vertical

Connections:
+3.3v: C108.1, C110.1, C111.1, C112.1, C114.1, JP201.1, JP202.1, JP203.1, JP301.1, JP302.1, JP303.1, JP401.1, JP402.1, JP403.1, JP501.1, JP502.1, JP503.1, P105.3, P106.1, P108.3, P109.3, R102.2, R104.2, R105.1, R106.1, R107.1, R202.2, R203.2, R302.2, R303.2, R402.2, R403.2, R502.2, R503.2, U102.2, U103.1, U103.13, U103.19, U103.32, U103.48, U103.64
+12v: C101.1, C202.2, C203.1, C204.1, C302.2, C303.1, C304.1, C402.2, C403.1, C404.1, C502.2, C503.1, C504.1, P101.1, P101.3, P102.1, P102.3, P102.5, P110.1, P110.2, P111.1, P601.1, R101.2, R201.2, R301.2, R401.2, R501.2, R703.2, R803.2, U201.16, U201.21, U301.16, U301.21, U401.16, U401.21, U501.16, U501.21
/+5v: C102.1, D103.1, P103.1, U101.5, U102.3
/BED_FET/OUT-: D801.1, P110.3, P110.4, Q801.2
/BED_PWM: R801.1, R802.2, U103.23
/BED_THERM: C117.2, P107.1, R106.2, U103.15
/CHIP_1_WIRE: U103.11, U105.17
/E0_DIR: U103.2, U501.14
/E0_ENABLE: R502.1, U103.4, U501.23
/E0_FET/OUT-: D701.1, P111.2, Q701.2
/E0_PWM: R701.1, R702.2, U103.37
/E0_STEP: U103.3, U501.11
/E0_THERM: C116.2, P104.1, R105.2, U103.14
/FAN_PWM: Q601.1, R601.1, U103.41
/NRST: P106.5, U103.7
/SWCLK: P106.2, U103.49
/SWDIO: P106.4, U103.46
/USART1_RX: U103.43, U105.43
/USART1_TX: U103.42, U105.45
/USB_DM: P103.2, U101.4, U103.44
/USB_DP: P103.3, R107.2, U101.3, U103.45
/X_DIR: U103.8, U201.14
/X_ENABLE: R202.1, U103.10, U201.23
/X_STEP: U103.9, U201.11
/X_STOP: P105.1, U103.56
/Y_DIR: U103.38, U301.14
/Y_ENABLE: R302.1, U103.40, U301.23
/Y_STEP: U103.39, U301.11
/Y_STOP: P108.1, U103.57
/Z_DIR: U103.34, U401.14
/Z_ENABLE: R402.1, U103.36, U401.23
/Z_STEP: U103.35, U401.11
/Z_STOP: P109.1, U103.61
GND: C101.2, C102.2, C103.2, C104.2, C108.2, C110.2, C111.2, C112.2, C113.2, C114.2, C116.1, C117.1, C203.2, C204.2, C303.2, C304.2, C403.2, C404.2, C503.2, C504.2, D101.1, D102.1, D601.2, JP101.1, P101.2, P101.4, P102.2, P102.4, P102.6, P103.5, P103.6, P104.2, P105.2, P106.3, P107.2, P108.2, P109.2, Q601.2, Q701.3, Q801.3, R204.2, R205.2, R304.2, R305.2, R404.2, R405.2, R504.2, R505.2, R601.2, R701.2, R801.2, RV201.3, RV301.3, RV401.3, RV501.3, U101.2, U102.1, U103.12, U103.18, U103.31, U103.47, U103.63, U105.1, U105.41, U201.8, U201.13, U201.24, U201.T, U301.8, U301.13, U301.24, U301.T, U401.8, U401.13, U401.24, U401.T, U501.8, U501.13, U501.24, U501.T
unnamed: C103.1, U103.5, Y101.1
unnamed: C104.1, R103.2, Y101.2
unnamed: C113.1, U103.30
unnamed: C201.1, U201.1
unnamed: C201.2, U201.2
unnamed: C202.1, U201.3
unnamed: C301.1, U301.1
unnamed: C301.2, U301.2
unnamed: C302.1, U301.3
unnamed: C401.1, U401.1
unnamed: C401.2, U401.2
unnamed: C402.1, U401.3
unnamed: C501.1, U501.1
unnamed: C501.2, U501.2
unnamed: C502.1, U501.3
unnamed: D101.2, R101.1
unnamed: D102.2, R102.1
unnamed: D103.2, U105.3
unnamed: D601.1, P601.2, Q601.3
unnamed: D701.2, R703.1
unnamed: D801.2, R803.1
unnamed: JP101.2, R104.1, U103.60
unnamed: JP201.2, U201.10
unnamed: JP202.2, U201.6
unnamed: JP203.2, U201.5
unnamed: JP301.2, U301.10
unnamed: JP302.2, U301.6
unnamed: JP303.2, U301.5
unnamed: JP401.2, U401.10
unnamed: JP402.2, U401.6
unnamed: JP403.2, U401.5
unnamed: JP501.2, U501.10
unnamed: JP502.2, U501.6
unnamed: JP503.2, U501.5
unnamed: P201.1, U201.15
unnamed: P201.2, U201.18
unnamed: P201.3, U201.19
unnamed: P201.4, U201.22
unnamed: P301.1, U301.15
unnamed: P301.2, U301.18
unnamed: P301.3, U301.19
unnamed: P301.4, U301.22
unnamed: P401.1, U401.15
unnamed: P401.2, U401.18
unnamed: P401.3, U401.19
unnamed: P401.4, U401.22
unnamed: P501.1, U501.15
unnamed: P501.2, U501.18
unnamed: P501.3, U501.19
unnamed: P501.4, U501.22
unnamed: Q701.1, R702.1
unnamed: Q801.1, R802.1
unnamed: R103.1, U103.6
unnamed: R201.1, RV201.1
unnamed: R203.1, U201.7, U201.9
unnamed: R204.1, U201.20
unnamed: R205.1, U201.17
unnamed: R301.1, RV301.1
unnamed: R303.1, U301.7, U301.9
unnamed: R304.1, U301.20
unnamed: R305.1, U301.17
unnamed: R401.1, RV401.1
unnamed: R403.1, U401.7, U401.9
unnamed: R404.1, U401.20
unnamed: R405.1, U401.17
unnamed: R501.1, RV501.1
unnamed: R503.1, U501.7, U501.9
unnamed: R504.1, U501.20
unnamed: R505.1, U501.17
unnamed: RV201.2, U201.12
unnamed: RV301.2, U301.12
unnamed: RV401.2, U401.12
unnamed: RV501.2, U501.12

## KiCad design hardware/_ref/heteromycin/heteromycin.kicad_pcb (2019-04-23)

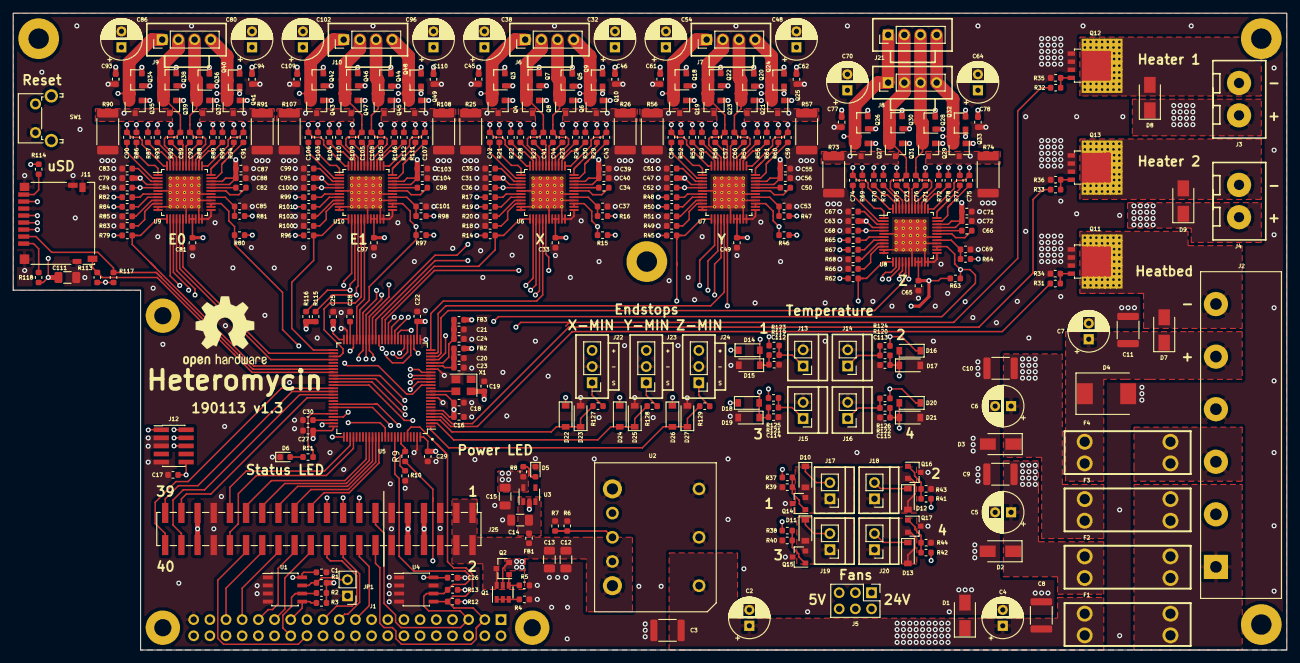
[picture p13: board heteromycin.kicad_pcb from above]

Board: 4 copper layers, 200.0 x 100.0 mm, 373 parts (1 on the bottom side), 293 nets.

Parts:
C1, C16, C17, C18, C19, C22, C23, C24, C25, C26, C27, C29, C31, C33, C39, C40, C47, C49, C55, C56, C63, C65, C71, C72, C79, C81, C87, C88, C95, C97, C103, C104, C112, C113, C114, C115: 100nF; C_0603_1608Metric
C2, C4, C5, C6, C7, C32, C38, C48, C54, C64, C70, C80, C86, C96, C102: 100uF; CP_Radial_D6.3mm_P2.50mm
C3, C8, C9, C10, C11: 100nF; C_1812_4532Metric
C12, C14: 22uF; C_1206_3216Metric
C13: 100nF; C_1206_3216Metric
C15, C111: 10uF; C_1206_3216Metric
C20, C21: 1uF; C_0603_1608Metric
C28, C30, C35, C36, C51, C52, C67, C68, C83, C84, C99, C100: 2.2uF; C_0603_1608Metric
C34, C50, C66, C82, C98: 22nF; C_0603_1608Metric
C37, C45, C46, C53, C61, C62, C69, C77, C78, C85, C93, C94, C101, C109, C110: 470nF; C_0603_1608Metric
C41, C42, C43, C44, C57, C58, C59, C60, C73, C74, C75, C76, C89, C90, C91, C92, C105, C106, C107, C108: 220nF; C_0603_1608Metric
D1, D2, D3: SMAJ28A; D_SMA
D4: S3A-13-F; D_SMC
D5: LTST-C194KGKT; LED_0603_1608Metric
D6: LTST-C194KSKT; LED_0603_1608Metric
D7, D8, D9: SK310A-LTP; D_SMA
D10, D11, D12, D13, D14, D15, D16, D17, D18, D19, D20, D21, D22, D23, D24, D25, D26, D27: BAT54GWJ; D_SOD-123
F1, F2, F3, F4: 3557-2; KEYSTONE-FUSE-3557-2
FB1, FB2, FB3: MPZ1608S221A; R_0603_1608Metric
H1, H2, H5: MountingHole_2.7mm_M2.5_Pad
H3, H4, H6, H7: MountingHole_3.2mm_M3_Pad
J1: M20-7832046; PinSocket_2x20_P2.54mm_Vertical
J2: 4DB-P108-06
J3, J4: 39531-1002
J5: Conn_02x03_Counter_Clockwise; PinHeader_2x03_P2.54mm_Vertical
J6, J7, J8, J9, J10, J21: 70543-0003
J11: DM3D-SF; microSD_HC_Hirose_DM3D-SF
J12: 20021121-00010C4LF; PinHeader_2x05_P1.27mm_Vertical_SMD
J13, J14, J15, J16, J17, J18, J19, J20: 70543-0001
J22, J23, J24: 70543-0002
J25: Conn_02x20_Odd_Even; PinHeader_2x20_P2.54mm_Vertical_SMD
JP1: Jumper_2_Open; PinHeader_1x02_P2.54mm_Vertical
LOGO1: Logo_Open_Hardware_Large; OSHW-Logo2_14.6x12mm_SilkScreen
Q1: DMMT5401; SOT-23-6
Q2: DMG2305UX; SOT-23
Q3, Q4, Q5, Q6, Q7, Q8, Q9, Q10, Q14, Q15, Q16, Q17, Q18, Q19, Q20, Q21, Q22, Q23, Q24, Q25, Q26, Q27, Q28, Q29, Q30, Q31, Q32, Q33, Q34, Q35, Q36, Q37, Q38, Q39, Q40, Q41, Q42, Q43, Q44, Q45, Q46, Q47, Q48, Q49: IRLML0030TRPbF; SOT-23
Q11, Q12, Q13: PSMN1R2-30YLC,115; SOT-669_LFPAK_ThermalVias-1
R1, R5, R14, R15, R45, R46, R62, R63, R79, R80, R96, R97, R113, R114, R115, R116, R117, R118: 47k; R_0603_1608Metric
R2, R3: 3.9K; R_0603_1608Metric
R4, R9: 10k; R_0603_1608Metric
R6: 20k; R_0603_1608Metric
R7: 15k; R_0603_1608Metric
R8, R11, R127, R128, R129: 1k; R_0603_1608Metric
R10, R34, R35, R36, R39, R40, R43, R44: 100k; R_0603_1608Metric
R12, R13, R119, R120, R121, R122, R123, R124, R125, R126: 4.7k; R_0603_1608Metric
R16, R47, R64, R81, R98: 2.2; R_0603_1608Metric
R17, R18, R19, R20, R48, R49, R50, R51, R65, R66, R67, R68, R82, R83, R84, R85, R99, R100, R101, R102: 47; R_0603_1608Metric
R21, R22, R23, R24, R27, R28, R29, R30, R52, R53, R54, R55, R58, R59, R60, R61, R69, R70, R71, R72, R75, R76, R77, R78, R86, R87, R88, R89, R92, R93, R94, R95, R103, R104, R105, R106, R109, R110, R111, R112: 10; R_0603_1608Metric
R25, R26, R56, R57, R73, R74, R90, R91, R107, R108: 0.1; R_2512_6332Metric
R31, R32, R33, R37, R38, R41, R42: 100; R_0603_1608Metric
SW1: PTS645VL39-2; SW_Tactile_SPST_Angled_PTS645Vx39-2LFS
U1, U4: CAT24C32; SOIC-8_3.9x4.9mm_P1.27mm
U2: i3A
U3: AP7365-33WG-7; SOT-23-5
U5: STM32H743VI; TQFP-100_14x14mm_P0.5mm
U6, U7, U8, U9, U10: TMC2160-TA; TQFP-48-1EP_7x7mm_P0.5mm_EP5x5mm_ThermalVias
X1: ECS-TXO-3225-250-TR; ECS-TXO-3225

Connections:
/Connectors/MCU_MISO: J11.7, J25.17, R115.1, U5.43, U6.16, U7.16, U8.16, U9.16, U10.16
/Connectors/MCU_MOSI: J11.3, J25.19, R116.1, U5.44, U6.15, U7.15, U8.15, U9.15, U10.15
/Connectors/MCU_SCK: J11.5, J25.15, U5.42, U6.14, U7.14, U8.14, U9.14, U10.14
/Connectors/PI_SCK: J1.23, J25.20, U5.29
/Connectors/PI_SS1: J1.26, J25.30
/Connectors/PWM_EXT1: J25.37, U5.66
/Connectors/PWM_EXT2: J25.38, U5.65
/Connectors/PWM_EXT3: J25.39, U5.64
/Connectors/PWM_EXT4: J25.40, U5.63
/Connectors/RX: J25.32, U5.79
/Connectors/SCL: J1.5, J25.13, R13.1, U4.6, U5.92
/Connectors/SDA: J1.3, J25.14, R12.1, U4.5, U5.96
/Connectors/SWCLK: J12.4, U5.76
/Connectors/SWDIO: J12.2, U5.72
/Connectors/SWO: J12.6, U5.89
/Connectors/TEMP1: C112.1, D14.2, D15.1, R119.2, U5.18
/Connectors/TEMP2: C113.1, D16.2, D17.1, R120.2, U5.17
/Connectors/TEMP3: C114.1, D18.2, D19.1, R121.2, U5.16
/Connectors/TEMP4: C115.1, D20.2, D21.1, R122.2, U5.15
/Connectors/TX: J25.31, U5.78
/Connectors/X_MIN: D22.2, D23.1, R127.2, U5.3
/Connectors/Y_MIN: D24.2, D25.1, R128.2, U5.2
/Connectors/Z_MIN: D26.2, D27.1, R129.2, U5.1
/Connectors/nRESET: C17.2, J1.12, J12.10, SW1.2, U5.14
/MCU/BOOT: J1.7, R9.1
/MCU/BOOTpin: R9.2, R10.2, U5.94
/MCU/CLK: U5.12, X1.3
/MCU/D1: J25.21, U5.87
/MCU/D2: J25.23, U5.86
/MCU/D3: J25.25, U5.85
/MCU/D4: J25.27, U5.84
/MCU/D5: J25.29, U5.83
/MCU/MCU_SS: J1.24, U5.28
/MCU/PWM_BED: R31.2, U5.4
/MCU/PWM_FAN1: R37.2, U5.59
/MCU/PWM_FAN2: R41.2, U5.60
/MCU/PWM_FAN3: R38.2, U5.61
/MCU/PWM_FAN4: R42.2, U5.62
/MCU/PWM_HEAT1: R32.2, U5.22
/MCU/PWM_HEAT2: R33.2, U5.5
/MCU/SD_DETECT: J11.10, R113.1, U5.58
/MCU/STATUS_LED: R11.1, U5.71
/MCU/VCAP1: C28.2, U5.48
/MCU/VCAP2: C30.2, U5.73
/MCU/VDDA: C21.1, C24.1, FB3.1, U5.21
/MCU/VREF+: C20.2, C23.2, FB2.1, U5.20
/Raspberry Pi Connector/D1: J1.29, J25.22
/Raspberry Pi Connector/D2: J1.31, J25.24
/Raspberry Pi Connector/D3: J1.33, J25.26
/Raspberry Pi Connector/D4: J1.35, J25.28
/Raspberry Pi Connector/ID_SC_EEPROM: J1.28, R2.2, U1.6
/Raspberry Pi Connector/ID_SD_EEPROM: J1.27, R3.2, U1.5
/Raspberry Pi Connector/MISO: J1.21, J25.18, U5.30
/Raspberry Pi Connector/MOSI: J1.19, J25.16, U5.31
/Raspberry Pi Connector/RX: J1.10, U5.68
/Raspberry Pi Connector/TX: J1.8, U5.69
/Raspberry Pi Connector/VDD5V_HAT: J1.2, J1.4, Q1.5, Q2.2
/SD Card Reader/SS: J11.2, R117.1, U5.57
/Steper Motor Y/5VOUT: C52.1, R47.2, U7.5
/Steper Motor Y/12VOUT: C51.1, U7.3
/Steper Motor Y/BMA1: C60.2, J7.3, Q20.3, Q21.2, U7.40
/Steper Motor Y/BMA2: C59.2, J7.4, Q24.3, Q25.2, U7.37
/Steper Motor Y/BMB1: C58.2, J7.1, Q18.3, Q19.2, U7.48
/Steper Motor Y/BMB2: C57.2, J7.2, Q22.3, Q23.2, U7.45
/Steper Motor Y/CA1: C60.1, U7.42
/Steper Motor Y/CA2: C59.1, U7.35
/Steper Motor Y/CB1: C58.1, U7.2
/Steper Motor Y/CB2: C57.1, U7.43
/Steper Motor Y/CPI: C50.1, U7.32
/Steper Motor Y/CPO: C50.2, U7.31
/Steper Motor Y/DIAG: R46.1, U5.40, U7.26, U7.27
/Steper Motor Y/DIR: U5.35, U7.18
/Steper Motor Y/HA1: R54.1, U7.41
/Steper Motor Y/HA2: R60.2, U7.36
/Steper Motor Y/HB1: R52.1, U7.1
/Steper Motor Y/HB2: R58.2, U7.44
/Steper Motor Y/LA1: R55.1, U7.39
/Steper Motor Y/LA2: R61.2, U7.38
/Steper Motor Y/LB1: R53.1, U7.47
/Steper Motor Y/LB2: R59.2, U7.46
/Steper Motor Y/SRAH: R50.1, U7.8
/Steper Motor Y/SRAL: R51.1, U7.9
/Steper Motor Y/SRBH: R48.2, U7.7
/Steper Motor Y/SRBL: R49.1, U7.10
/Steper Motor Y/SS: R45.1, U5.36, U7.13
/Steper Motor Y/STEP: U5.24, U7.17
/Steper Motor Y/VCC: C53.1, R47.1, U7.29
/Stepper Motor E0/5VOUT: C84.1, R81.2, U9.5
/Stepper Motor E0/12VOUT: C83.1, U9.3
/Stepper Motor E0/BMA1: C92.2, J9.3, Q36.3, Q37.2, U9.40
/Stepper Motor E0/BMA2: C91.2, J9.4, Q40.3, Q41.2, U9.37
/Stepper Motor E0/BMB1: C90.2, J9.1, Q34.3, Q35.2, U9.48
/Stepper Motor E0/BMB2: C89.2, J9.2, Q38.3, Q39.2, U9.45
/Stepper Motor E0/CA1: C92.1, U9.42
/Stepper Motor E0/CA2: C91.1, U9.35
/Stepper Motor E0/CB1: C90.1, U9.2
/Stepper Motor E0/CB2: C89.1, U9.43
/Stepper Motor E0/CPI: C82.1, U9.32
/Stepper Motor E0/CPO: C82.2, U9.31
/Stepper Motor E0/DIAG: R80.1, U5.47, U9.26, U9.27
/Stepper Motor E0/DIR: U5.52, U9.18
/Stepper Motor E0/HA1: R88.1, U9.41
/Stepper Motor E0/HA2: R94.2, U9.36
/Stepper Motor E0/HB1: R86.1, U9.1
/Stepper Motor E0/HB2: R92.2, U9.44
/Stepper Motor E0/LA1: R89.1, U9.39
/Stepper Motor E0/LA2: R95.2, U9.38
/Stepper Motor E0/LB1: R87.1, U9.47
/Stepper Motor E0/LB2: R93.2, U9.46
/Stepper Motor E0/SRAH: R84.1, U9.8
/Stepper Motor E0/SRAL: R85.1, U9.9
/Stepper Motor E0/SRBH: R82.2, U9.7
/Stepper Motor E0/SRBL: R83.1, U9.10
/Stepper Motor E0/SS: R79.1, U5.56, U9.13
/Stepper Motor E0/STEP: U5.54, U9.17
/Stepper Motor E0/VCC: C85.1, R81.1, U9.29
/Stepper Motor E1/5VOUT: C100.1, R98.2, U10.5
/Stepper Motor E1/12VOUT: C99.1, U10.3
/Stepper Motor E1/BMA1: C108.2, J10.3, Q44.3, Q45.2, U10.40
/Stepper Motor E1/BMA2: C107.2, J10.4, Q48.3, Q49.2, U10.37
/Stepper Motor E1/BMB1: C106.2, J10.1, Q42.3, Q43.2, U10.48
/Stepper Motor E1/BMB2: C105.2, J10.2, Q46.3, Q47.2, U10.45
/Stepper Motor E1/CA1: C108.1, U10.42
/Stepper Motor E1/CA2: C107.1, U10.35
/Stepper Motor E1/CB1: C106.1, U10.2
/Stepper Motor E1/CB2: C105.1, U10.43
/Stepper Motor E1/CPI: C98.1, U10.32
/Stepper Motor E1/CPO: C98.2, U10.31
/Stepper Motor E1/DIAG: R97.1, U5.45, U10.26, U10.27
/Stepper Motor E1/DIR: U5.46, U10.18
/Stepper Motor E1/HA1: R105.1, U10.41
/Stepper Motor E1/HA2: R111.2, U10.36
/Stepper Motor E1/HB1: R103.1, U10.1
/Stepper Motor E1/HB2: R109.2, U10.44
/Stepper Motor E1/LA1: R106.1, U10.39
/Stepper Motor E1/LA2: R112.2, U10.38
/Stepper Motor E1/LB1: R104.1, U10.47
/Stepper Motor E1/LB2: R110.2, U10.46
/Stepper Motor E1/SRAH: R101.1, U10.8
/Stepper Motor E1/SRAL: R102.1, U10.9
/Stepper Motor E1/SRBH: R99.2, U10.7
/Stepper Motor E1/SRBL: R100.1, U10.10
/Stepper Motor E1/SS: R96.1, U5.51, U10.13
/Stepper Motor E1/STEP: U5.53, U10.17
/Stepper Motor E1/VCC: C101.1, R98.1, U10.29
/Stepper Motor X/5VOUT: C36.1, R16.2, U6.5
/Stepper Motor X/12VOUT: C35.1, U6.3
/Stepper Motor X/BMA1: C44.2, J6.3, Q5.3, Q6.2, U6.40
/Stepper Motor X/BMA2: C43.2, J6.4, Q9.3, Q10.2, U6.37
/Stepper Motor X/BMB1: C42.2, J6.1, Q3.3, Q4.2, U6.48
/Stepper Motor X/BMB2: C41.2, J6.2, Q7.3, Q8.2, U6.45
/Stepper Motor X/CA1: C44.1, U6.42
/Stepper Motor X/CA2: C43.1, U6.35
/Stepper Motor X/CB1: C42.1, U6.2
/Stepper Motor X/CB2: C41.1, U6.43
/Stepper Motor X/CPI: C34.1, U6.32
/Stepper Motor X/CPO: C34.2, U6.31
/Stepper Motor X/DIAG: R15.1, U5.41, U6.26, U6.27
/Stepper Motor X/DIR: U5.37, U6.18
/Stepper Motor X/HA1: R23.1, U6.41
/Stepper Motor X/HA2: R29.2, U6.36
/Stepper Motor X/HB1: R21.1, U6.1
/Stepper Motor X/HB2: R27.2, U6.44
/Stepper Motor X/LA1: R24.1, U6.39
/Stepper Motor X/LA2: R30.2, U6.38
/Stepper Motor X/LB1: R22.1, U6.47
/Stepper Motor X/LB2: R28.2, U6.46
/Stepper Motor X/SRAH: R19.1, U6.8
/Stepper Motor X/SRAL: R20.1, U6.9
/Stepper Motor X/SRBH: R17.2, U6.7
/Stepper Motor X/SRBL: R18.1, U6.10
/Stepper Motor X/SS: R14.1, U5.38, U6.13
/Stepper Motor X/STEP: U5.25, U6.17
/Stepper Motor X/VCC: C37.1, R16.1, U6.29
/Stepper Motor Z/5VOUT: C68.1, R64.2, U8.5
/Stepper Motor Z/12VOUT: C67.1, U8.3
/Stepper Motor Z/BMA1: C76.2, J8.3, J21.3, Q28.3, Q29.2, U8.40
/Stepper Motor Z/BMA2: C75.2, J8.4, J21.4, Q32.3, Q33.2, U8.37
/Stepper Motor Z/BMB1: C74.2, J8.1, J21.1, Q26.3, Q27.2, U8.48
/Stepper Motor Z/BMB2: C73.2, J8.2, J21.2, Q30.3, Q31.2, U8.45
/Stepper Motor Z/CA1: C76.1, U8.42
/Stepper Motor Z/CA2: C75.1, U8.35
/Stepper Motor Z/CB1: C74.1, U8.2
/Stepper Motor Z/CB2: C73.1, U8.43
/Stepper Motor Z/CPI: C66.1, U8.32
/Stepper Motor Z/CPO: C66.2, U8.31
/Stepper Motor Z/DIAG: R63.1, U5.39, U8.26, U8.27
/Stepper Motor Z/DIR: U5.33, U8.18
/Stepper Motor Z/HA1: R71.1, U8.41
/Stepper Motor Z/HA2: R77.2, U8.36
/Stepper Motor Z/HB1: R69.1, U8.1
/Stepper Motor Z/HB2: R75.2, U8.44
/Stepper Motor Z/LA1: R72.1, U8.39
/Stepper Motor Z/LA2: R78.2, U8.38
/Stepper Motor Z/LB1: R70.1, U8.47
/Stepper Motor Z/LB2: R76.2, U8.46
/Stepper Motor Z/SRAH: R67.1, U8.8
/Stepper Motor Z/SRAL: R68.1, U8.9
/Stepper Motor Z/SRBH: R65.2, U8.7
/Stepper Motor Z/SRBL: R66.1, U8.10
/Stepper Motor Z/SS: R62.1, U5.34, U8.13
/Stepper Motor Z/STEP: U5.23, U8.17
/Stepper Motor Z/VCC: C69.1, R64.1, U8.29
BED_OUT: D7.2, J2.6, Q11.5
FAN1_OUT: D10.2, J17.1, Q14.2
FAN2_OUT: D12.2, J18.1, Q16.2
FAN3_OUT: D11.2, J19.1, Q15.2
FAN4_OUT: D13.2, J20.1, Q17.2
GND: C1.2, C2.2, C3.2, C4.2, C5.2, C6.2, C7.2, C8.2, C9.2, C10.2, C11.2, C12.2, C13.2, C14.2, C15.2, C16.2, C17.1, C18.2, C19.2, C20.1, C21.2, C22.2, C23.1, C24.2, C25.2, C26.2, C27.2, C28.1, C29.2, C30.1, C31.2, C32.2, C33.2, C35.2, C36.2, C37.2, C38.2, C39.2, C40.2, C45.2, C46.2, C47.2, C48.2, C49.2, C51.2, C52.2, C53.2, C54.2, C55.2, C56.2, C61.2, C62.2, C63.2, C64.2, C65.2, C67.2, C68.2, C69.2, C70.2, C71.2, C72.2, C77.2, C78.2, C79.2, C80.2, C81.2, C83.2, C84.2, C85.2, C86.2, C87.2, C88.2, C93.2, C94.2, C95.2, C96.2, C97.2, C99.2, C100.2, C101.2, C102.2, C103.2, C104.2, C109.2, C110.2, C111.2, C112.2, C113.2, C114.2, C115.2, D1.2, D2.2, D3.2, D4.2, D5.1, D6.1, D15.2, D17.2, D19.2, D21.2, D23.2, D25.2, D27.2, J1.6, J1.9, J1.14, J1.20, J1.25, J1.30, J1.34, J1.39, J2.2, J2.4, J11.6, J11.9, J11.11, J12.3, J12.5, J12.9, J13.2, J14.2, J15.2, J16.2, J22.2, J23.2, J24.2, J25.5, J25.6, J25.11, J25.12, J25.33, J25.34, JP1.1, Q11.1, Q11.2, Q11.3, Q12.1, Q12.2, Q12.3, Q13.1, Q13.2, Q13.3, Q14.3, Q15.3, Q16.3, Q17.3, R4.2, R5.2, R6.2, R7.2, R10.1, R18.2, R20.2, R25.1, R26.1, R34.1, R35.1, R36.1, R39.1, R40.1, R43.1, R44.1, R49.2, R51.2, R56.1, R57.1, R66.2, R68.2, R73.1, R74.1, R83.2, R85.2, R90.1, R91.1, R100.2, R102.2, R107.1, R108.1, SW1.1, U1.1, U1.2, U1.3, U1.4, U2.2, U2.3, U2.4, U3.2, U4.1, U4.2, U4.3, U4.4, U4.7, U5.10, U5.19, U5.26, U5.49, U5.74, U5.99, U6.6, U6.11, U6.12, U6.19, U6.23, U6.24, U6.25, U6.28, U6.30, U6.49, U7.6, U7.11, U7.12, U7.19, U7.23, U7.24, U7.25, U7.28, U7.30, U7.49, U8.6, U8.11, U8.12, U8.19, U8.23, U8.24, U8.25, U8.28, U8.30, U8.49, U9.6, U9.11, U9.12, U9.19, U9.23, U9.24, U9.25, U9.28, U9.30, U9.49, U10.6, U10.11, U10.12, U10.19, U10.23, U10.24, U10.25, U10.28, U10.30, U10.49, X1.2
HEAT1_OUT: D8.2, J3.1, Q12.5
HEAT2_OUT: D9.2, J4.1, Q13.5
unnamed: C14.1, FB1.1, U3.1, U3.3
unnamed: D5.2, R8.2
unnamed: D6.2, R11.2
unnamed: F1.2, F2.2, F3.2, J2.1
unnamed: F4.2, J2.3
unnamed: J11.1, R118.1
unnamed: J11.8, R114.1
unnamed: J13.1, R119.1, R123.2
unnamed: J14.1, R120.1, R124.2
unnamed: J15.1, R121.1, R125.2
unnamed: J16.1, R122.1, R126.2
unnamed: J22.1, R127.1
unnamed: J23.1, R128.1
unnamed: J24.1, R129.1
unnamed: JP1.2, R1.1, U1.7
unnamed: Q1.1, Q1.2, Q1.3, R4.1
unnamed: Q1.4, Q2.1, R5.1
unnamed: Q3.1, R21.2
unnamed: Q4.1, R22.2
unnamed: Q4.3, Q8.3, R17.1, R25.2
unnamed: Q5.1, R23.2
unnamed: Q6.1, R24.2
unnamed: Q7.1, R27.1
unnamed: Q8.1, R28.1
unnamed: Q9.1, R29.1
unnamed: Q10.1, R30.1
unnamed: Q6.3, Q10.3, R19.2, R26.2
unnamed: Q11.4, R31.1, R34.2
unnamed: Q12.4, R32.1, R35.2
unnamed: Q13.4, R33.1, R36.2
unnamed: Q14.1, R37.1, R39.2
unnamed: Q15.1, R38.1, R40.2
unnamed: Q16.1, R41.1, R43.2
unnamed: Q17.1, R42.1, R44.2
unnamed: Q18.1, R52.2
unnamed: Q19.1, R53.2
unnamed: Q19.3, Q23.3, R48.1, R56.2
unnamed: Q20.1, R54.2
unnamed: Q21.1, R55.2
unnamed: Q21.3, Q25.3, R50.2, R57.2
unnamed: Q22.1, R58.1
unnamed: Q23.1, R59.1
unnamed: Q24.1, R60.1
unnamed: Q25.1, R61.1
unnamed: Q26.1, R69.2
unnamed: Q27.1, R70.2
unnamed: Q27.3, Q31.3, R65.1, R73.2
unnamed: Q28.1, R71.2
unnamed: Q29.1, R72.2
unnamed: Q29.3, Q33.3, R67.2, R74.2
unnamed: Q30.1, R75.1
unnamed: Q31.1, R76.1
unnamed: Q32.1, R77.1
unnamed: Q33.1, R78.1
unnamed: Q34.1, R86.2
unnamed: Q35.1, R87.2
unnamed: Q35.3, Q39.3, R82.1, R90.2
unnamed: Q36.1, R88.2
unnamed: Q37.1, R89.2
unnamed: Q37.3, Q41.3, R84.2, R91.2
unnamed: Q38.1, R92.1
unnamed: Q39.1, R93.1
unnamed: Q40.1, R94.1
unnamed: Q41.1, R95.1
unnamed: Q42.1, R103.2
unnamed: Q43.1, R104.2
unnamed: Q43.3, Q47.3, R99.1, R107.2
unnamed: Q44.1, R105.2
unnamed: Q45.1, R106.2
unnamed: Q45.3, Q49.3, R101.2, R108.2
unnamed: Q46.1, R109.1
unnamed: Q47.1, R110.1
unnamed: Q48.1, R111.1
unnamed: Q49.1, R112.1
unnamed: R6.1, R7.1, U2.6
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

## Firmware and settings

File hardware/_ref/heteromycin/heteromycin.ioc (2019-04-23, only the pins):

Mcu.UserName=STM32H743VITx
PA0.GPIO_Label=PWM_HEAT1
PA0.Signal=S_TIM2_CH1
PA1.GPIO_Label=STEP_Z
PA1.Signal=S_TIM2_CH2
PA10.Signal=USART1_RX
PA12.GPIO_Label=STATUS_LED
PA12.Signal=GPIO_Output
PA2.GPIO_Label=STEP_Y
PA2.Signal=S_TIM2_CH3
PA3.GPIO_Label=STEP_X
PA3.Signal=S_TIM2_CH4
PA4.GPIO_Label=MCU_SS
PA4.Signal=SPI1_NSS
PA5.Signal=SPI1_SCK
PA6.Signal=SPI1_MISO
PA7.Signal=SPI1_MOSI
PA9.Signal=USART1_TX
PB0.GPIO_Label=SS_Z
PB0.Signal=GPIO_Output
PB1.GPIO_Label=DIR_Y
PB1.Signal=GPIO_Output
PB10.GPIO_Label=DIR_E1
PB10.Signal=GPIO_Output
PB11.GPIO_Label=DIAG_E0
PB11.Signal=GPIO_Input
PB12.GPIO_Label=SS_E1
PB12.Signal=GPIO_Output
PB13.GPIO_Label=DIR_E0
PB13.Signal=GPIO_Output
PB14.GPIO_Label=STEP_E1
PB14.Signal=S_TIM12_CH1
PB15.GPIO_Label=STEP_E0
PB15.Signal=S_TIM12_CH2
PB2.GPIO_Label=SS_Y
PB2.Signal=GPIO_Output
PB6.Signal=I2C1_SCL
PB9.Signal=I2C1_SDA
PC0.GPIO_Label=TEMP4
PC0.Signal=ADCx_INP10
PC1.GPIO_Label=TEMP3
PC1.Signal=ADCx_INP11
PC10.Signal=USART3_TX
PC11.Signal=USART3_RX
PC2_C.GPIO_Label=TEMP2
PC2_C.Signal=ADC3_INP0
PC3_C.GPIO_Label=TEMP1
PC3_C.Signal=ADC3_INP1
PC5.GPIO_Label=DIR_Z
PC5.Signal=GPIO_Output
PC6.GPIO_Label=PWM_EXT4
PC6.Signal=S_TIM3_CH1
PC7.GPIO_Label=PWM_EXT3
PC7.Signal=S_TIM3_CH2
PC8.GPIO_Label=PWM_EXT2
PC8.Signal=S_TIM3_CH3
PC9.GPIO_Label=PWM_EXT1
PC9.Signal=S_TIM3_CH4
PD10.GPIO_Label=SS_SD
PD10.Signal=GPIO_Output
PD11.GPIO_Label=SD_DETECT
PD11.Signal=GPIO_Input
PD12.GPIO_Label=PWM_FAN1
PD12.Signal=S_TIM4_CH1
PD13.GPIO_Label=PWM_FAN2
PD13.Signal=S_TIM4_CH2
PD14.GPIO_Label=PWM_FAN3
PD14.Signal=S_TIM4_CH3
PD15.GPIO_Label=PWM_FAN4
PD15.Signal=S_TIM4_CH4
PD2.GPIO_Label=D5
PD2.Signal=GPIO_Input
PD3.GPIO_Label=D4
PD3.Signal=GPIO_Input
PD4.GPIO_Label=D3
PD4.Signal=GPIO_Input
PD5.GPIO_Label=D2
PD5.Signal=GPIO_Input
PD6.GPIO_Label=D1
PD6.Signal=GPIO_Input
PD9.GPIO_Label=SS_E0
PD9.Signal=GPIO_Output
PE10.GPIO_Label=DIAG_Y
PE10.Signal=GPIO_Input
PE11.GPIO_Label=DIAG_X
PE11.Signal=GPIO_Input
PE12.Signal=SPI4_SCK
PE13.Signal=SPI4_MISO
PE14.Signal=SPI4_MOSI
PE15.GPIO_Label=DIAG_E1
PE15.Signal=GPIO_Input
PE2.GPIO_Label=Z_MIN
PE2.Signal=GPIO_Input
PE3.GPIO_Label=Y_MIN
PE3.Signal=GPIO_Input
PE4.GPIO_Label=X_MIN
PE4.Signal=GPIO_Input
PE5.GPIO_Label=PWM_BED
PE5.Signal=S_TIM15_CH1
PE6.GPIO_Label=PWM_HEAT2
PE6.Signal=S_TIM15_CH2
PE7.GPIO_Label=DIR_X
PE7.Signal=GPIO_Output
PE8.GPIO_Label=SS_X
PE8.Signal=GPIO_Output
PE9.GPIO_Label=DIAG_Z
PE9.Signal=GPIO_Input

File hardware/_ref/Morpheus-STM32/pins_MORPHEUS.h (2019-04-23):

/**
 * Marlin 3D Printer Firmware
 * Copyright (C) 2016 MarlinFirmware [https://github.com/MarlinFirmware/Marlin]
 *
 * Based on Sprinter and grbl.
 * Copyright (C) 2011 Camiel Gubbels / Erik van der Zalm
 *
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
 */

 /**
  * 2017 Victor Perez Marlin for stm32f1 test
  * 2018 Modified by Pablo Crespo for Morpheus Board (https://github.com/pscrespo/Morpheus-STM32)
  */

//
// MORPHEUS Board pin assignments
//

#ifndef __STM32F1__
  #error "Oops!  Make sure you have an STM32F1 board selected from the 'Tools -> Boards' menu."
#endif

#define BOARD_NAME "Bluepill based board"

//
// Limit Switches
//
#define X_MIN_PIN          PB14
#define Y_MIN_PIN          PB13
#define Z_MIN_PIN          PB12

//
// Z Probe (when not Z_MIN_PIN)
//
#ifndef Z_MIN_PROBE_PIN
  #define Z_MIN_PROBE_PIN  PB9
#endif

//
// Steppers
//
// X & Y enable are the same
#define X_STEP_PIN         PB7
#define X_DIR_PIN          PB6
#define X_ENABLE_PIN       PB8

#define Y_STEP_PIN         PB5
#define Y_DIR_PIN          PB4
#define Y_ENABLE_PIN       PB8

#define Z_STEP_PIN         PA15
#define Z_DIR_PIN          PA10
#define Z_ENABLE_PIN       PB3

#define E0_STEP_PIN        PA8
#define E0_DIR_PIN         PB15
#define E0_ENABLE_PIN      PA9

//
// Temperature Sensors
//
#define TEMP_0_PIN         PB1   // Analog Input (HOTEND thermistor)
#define TEMP_BED_PIN       PB0   // Analog Input (BED thermistor)

//
// Heaters / Fans
//
#define HEATER_0_PIN       PA2   // HOTEND MOSFET
#define HEATER_BED_PIN     PA0   // BED MOSFET

#define FAN_PIN            PA1   // FAN1 header on board - PRINT FAN

//
// Misc.
//
#define LED_PIN            PC13
#define SDSS               PA3

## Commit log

2019-04-26 update to add indicator for end-stop,
    [END_STOP.sch]
2019-04-27 update for endstop circuit,
    [END_STOP.sch]
2019-04-27 update to reverse NO/NC,
    [END_STOP.sch]
2019-04-27 update for stepper motor circuit,
    [E0_STEPPER_DRIVER.sch, E1_STEPPER_DRIVER.sch, E2_STEPPER_DRIVER.sch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]
2019-04-27 update to remove E3,
    [E0_STEPPER_DRIVER.sch, E1_STEPPER_DRIVER.sch, E2_STEPPER_DRIVER.sch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]
2019-04-27 update label,
    [E0_STEPPER_DRIVER.sch, E1_STEPPER_DRIVER.sch, END_STOP.sch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]
2019-04-27 update power supply circuit,
    [E0_STEPPER_DRIVER.sch, E1_STEPPER_DRIVER.sch, END_STOP.sch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]
2019-04-27 update hotend MOSFET,
    [FAN0.sch, FAN2.sch, HOTEND_0.sch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]
2019-04-27 update power tree,
    [LM2596HV_breakout.sch, POWER_TREE.sch, STM32_CORE.sch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]
2019-04-27 need to verify i2c circuit,
    [I2C.sch]
2019-04-27 update stm32-core,
    [HEATBED.sch, POWER_SUPPLY.sch, POWER_TREE.sch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]
2019-04-27 update annotations,
    [E0_STEPPER_DRIVER.sch, E1_STEPPER_DRIVER.sch, END_STOP.sch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]
2019-04-27 update power circuit,
    [STM32_CORE_POWER.dsn, STM32_CORE_POWER.kicad_pcb]
2019-04-28 update heater layouts,
    [HOTEND_0.dsn, HOTEND_0.kicad_pcb, HOTEND_0.sch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]
2019-04-28 update hotend pcb,
    [HOTEND_0.kicad_pcb]
2019-04-28 update hotend,
    [HOTEND_1.sch, HOTEND_2.dsn, HOTEND_2.kicad_pcb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]
2019-04-28 update heatbed,
    [HEATBED.sch]
2019-04-29 update for usb pull up resistor,
    [HEATBED.sch, HOTEND_0.sch, HOTEND_1.sch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]
2019-04-30 update power,
    [HEATBED.sch, I2C.sch, MP2303A_power_supply_5V.sch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]
2019-04-30 update for fans,
    [FAN0.sch, FAN1.kicad_pcb, FAN1.sch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]
2019-04-30 update for power circuits,
    [HEATBED.kicad_pcb, HOTEND_0.kicad_pcb, HOTEND_0.sch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]
2019-05-01 fix min/max stop footprint,
    [END_STOP.sch, Thermistors.sch, printer-board.kicad_pcb]
2019-05-01 fix termistor cap footprint,
    [printer-board.kicad_pcb]
2019-05-01 remove jumper in display FPC,
    [Thermistors.sch]
2019-05-01 update to re-annotation,
    [E0_STEPPER_DRIVER.sch, E1_STEPPER_DRIVER.sch, END_STOP.sch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]
2019-05-01 update for stepper Z,
    [E0_STEPPER_DRIVER.kicad_pcb, E1_STEPPER_DRIVER.kicad_pcb, E3_STEPPER_DRIVER.kicad_pcb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]
2019-05-01 update hotend footprint,
    [FAN0.dsn, FAN0.kicad_pcb, FAN1.dsn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]
2019-05-02 update positino,
    [HOTEND_0.sch, MP2303A_power_supply_3V3.dsn, MP2303A_power_supply_3V3.kicad_pcb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]
2019-05-02 fix 3v3 and 5v connected,
    [MP2303A_power_supply_5V.sch, POWER_SUPPLY.sch, POWER_TREE.sch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]
2019-05-02 remove unnecessary capacitor,
    [POWER_TREE.sch]
2019-05-02 update step motor terminal orientation,
    [E0_STEPPER_DRIVER.sch, E1_STEPPER_DRIVER.sch, END_STOP.dsn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]
2019-05-02 update driver position,
    [printer-board.kicad_pcb]
2019-05-02 update driver positin,
    [X_STEPPER_DRIVER.sch, orange_pi.sch, printer-board.kicad_pcb]
2019-05-02 update ROUTING,
    [E0_STEPPER_DRIVER.sch, E1_STEPPER_DRIVER.sch, END_STOP.sch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]

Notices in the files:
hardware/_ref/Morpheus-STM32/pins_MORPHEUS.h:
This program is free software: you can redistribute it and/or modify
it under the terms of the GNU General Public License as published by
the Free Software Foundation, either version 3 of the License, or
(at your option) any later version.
